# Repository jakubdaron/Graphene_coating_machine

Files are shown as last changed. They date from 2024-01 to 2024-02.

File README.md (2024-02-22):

429411629_411741121228787_1074731807515884978_n (1)

**Graphene coating machine**

In this project we showcase a budget machine for creating graphene coatings on work surfaces of wire forming die based on technology described in patent  PL 239477.

The machine was built using budget and easly accessible components as well as 3D printed parts. 
It consists of a linear Z-axis and a turntable that is outfited with pressure sensor and allows for full 360deg rotation.
Z axis allows the electrode to put pressure on the die in range of 0,5 - 5kg, set by user. 
Pressure sensor readings allow the pressure to be in range of 5 - 15% error tolerance depending on the quallity of sensor calibration.

DISCLAIMER:
Presented machine is an academic proof of concept and is not sutable for industrial aplication in it's current version. 
This project was done on behest and with guidance from patent owner for the technology as a proof of concept.

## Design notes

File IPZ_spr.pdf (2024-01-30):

# Urządzenie do nakładania powłok grafenowych na powierzchnię roboczą ciągadła stalowego

# Interdyscyplinarny projekt zespołowy 2023/24 Mechatronika - II stopień

Prowadzący Projektu:
Dr hab. inż. Zbigniew Zimniak Autorzy:
Jakub Daroń
Michał Dubaniewicz
Piotr Grabowski
Wojciech Kargul
Jan Konior
Mateusz Lisoń

## 1. Wstęp

W procesie ciągnienia drutów na ciągarkach wykorzystywane narzędzia – ciągadła – są poddawane są znaczącym siłą i z czasem degenerują pod wpływem ścierania. Z tego tytułu stosuje się materiały wysoce odporne na ścieranie do pokrycia powierzchni stożka roboczego. Typowe stosowane materiały to diament i węgliki spiekane. Na Rys. 1 przedstawiono schemat budowy ciągadła.

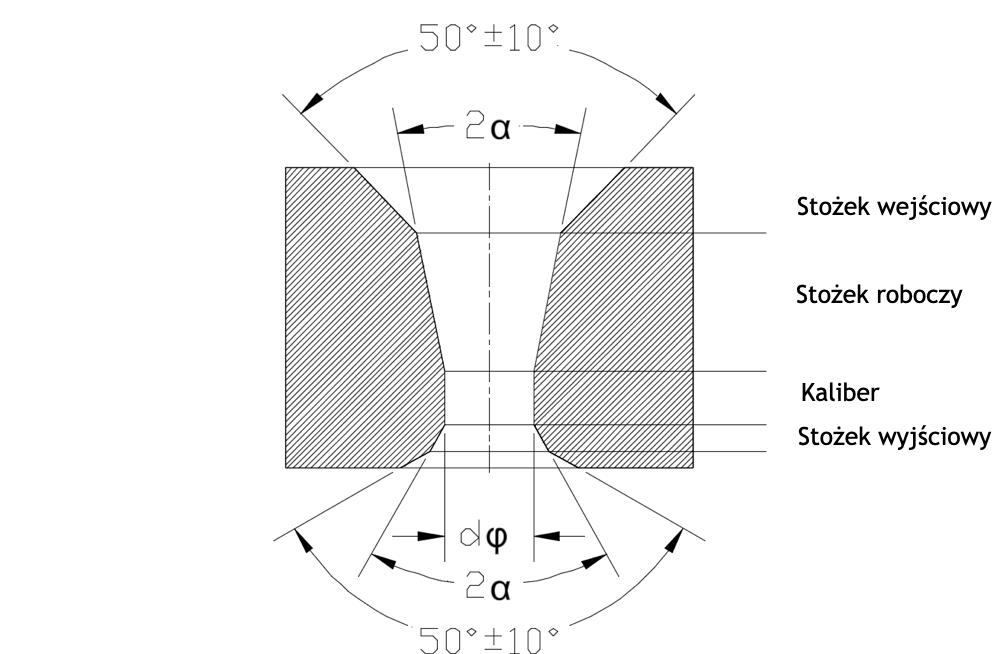
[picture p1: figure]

Rysunek 1 - schemat budowy ciągadła
Prowadzący projektu, dr hab. inż. Zbigniew Zimniak w swoim patencie nr PL 239477, zatytułowanym „Sposób wytwarzania trwałych cienkowarstwowych pokryć grafenowych na metalach” opisał metodę wytwarzania pokryć cienkowarstwowych z grafenu na metalach. Jak wiadomo grafen jest materiałem wysoce odpornym na ścieranie, w ramach projektu postanowiono zatem stworzyć urządzenie które pozwoli wykorzystać tą metodę do wykonywania powłok na elementach roboczych ciągadła stalowego.
W związku z tym określono następujące założenia projektowe:
- Minimalizacja kosztów – ze względu na brak funduszy wszystkie środki pochodzić będą z kieszeni wykonawców, określono budżet na poziomie ok. 600 zł.
- Maksymalizacja wykorzystania elementów typowych i wykonanych metodą druku 3D – ze względu na charakter naukowy budowanego urządzenia i niski budżet pewne elementy mogą wymagać wymiany lub modyfikacji z czasem. Zastosowanie druku 3D i elementów typowych ułatwi pracę w tego typu sytuacjach.
- 1 oś przesuwu liniowego pozwalająca uzyskać nacisk ok. 2kg, siła nacisku musi być sterowalna w pewnym zakresie – Parametry nacisku są powiązane z wymaganiami procesu nakładania powłok.

- 1 oś obrotowa – umożliwia obrót ciągadła i podział obrotu na x cykli w celu powtórzenia operacji pokrywania w innych pozycjach.
- Operacja półautomatyczna – ze względu na to że zasilacz generujący wyładowanie elektryczne jest stosowany również w innych instalacjach zdecydowano że nie będzie on sterowany z urządzenia tylko wyzwalany ręcznie.
- Sterowanie za pomocą aplikacji okienkowej – ze względu na ograniczanie kosztów zrezygnowano z fizycznego sterowania.

## 2. Przegląd Rozwiązań

Ze względu na to że urządzenie nie realizuje szeroko rozpowszechnionego procesu, nie ma rozwiązań które można wykorzystać jako bezpośrednie odniesienie. Z tego powodu poszczególne elementy projektu odnoszono do różnych urządzeń.
W przypadku osi przesuwu liniowego, jednym z bardziej powszechnych rozwiązań tego typu są drukarki 3D. Wykorzystują one śruby trapezowa lub kulowe drobnozwojne w celu uzyskania dokładności pozycjonowania. Całość jest napędzana napędami krokowymi. Przykład takiego urządzenia przedstawiono na Rys. 2.

Rysunek 2 - Przykładowa drukarka 3D (Prusa MINI+)

Innym przykładem urządzenia które przewijało się jako potencjalna inspiracja w przypadku przesuwu liniowego jest wiertarka kolumnowa, ze względu na to że są to konstrukcje przenoszące duże obciążenia. Na Rys. 3 przedstawiono przykładową konstrukcję.

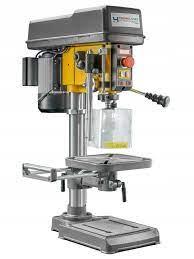
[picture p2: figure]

Rysunek 3 - przykładowa wiertarka kolumnowa
Ostatecznie, w przypadku projektowanego urządzenia konieczne będzie częściowe połączenie konkretnych cech obu rozwiązań – precyzji drukarek 3D i wytrzymałości którą cechuje się konstrukcja wiertarki kolumnowej.

W przypadku osi obrotowej, ciekawą inspiracją były stoły obrotowe do frezarek CNC (Rys. 4). Urządzenia te pozwalają uzyskać obrót o zadany kąt i są sterowane. Kwestią którą należy rozwiązać w celu adaptacji tego typu rozwiązania do projektu jest rozmiar i metoda mocowania obiektu w sposób zapewniający centryczność ciągadła i elektrody.

Rysunek 4 - przykładowy stół obrotowy do frezarki CNC

W przypadku pomiaru nacisku, na rynku są dostępne 2 główne rodzaje rozwiązań – czujniki membranowe i belki tensometryczne (Rys. 5). Belki tensometryczne pozwalają na uzyskanie odczytów dla dużych nacisków (powyżej 10 kg), natomiast zajmują dużo miejsca i w zastosowaniu takim jak w projekcie konieczne byłoby wykorzystanie minimum 2 takich belek. Czujniki membranowe z kolei są nieco bardziej wrażliwe na punkt przyłożenia siły i z reguły mają niższe zakresy pracy.

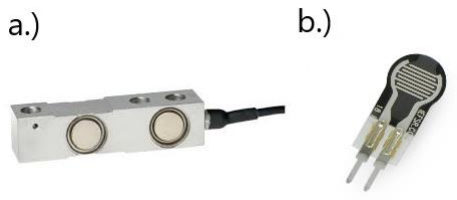
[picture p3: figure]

Rysunek 5 - a.) belka tensometryczna b.) czujnik membranowy

## 3. Sekcja Mechaniczna

### a. Ruch w osi pionowej

Pierwszym zagadnieniem mechanicznym do realizacji było zapewnienie ruchu elektrody w osi pionowej, jednocześnie z możliwością generowania jej docisku do ciągadła z siłą odpowiadającą wartości 2 [N]. W tym celu zamówiono prowadnicę liniową THK KR20A 200mm CNC o skoku śruby wynoszącym 1[mm] (Rys. 6). Ruch obrotowy śruby będzie generowany za pomocą silnika krokowego JK42HS40 – 0404, który zostanie szerzej przedstawiony w sekcji elektronicznej.

Rysunek 6 - Prowadnica liniowa THK KR20A 200 mm CNC
Szkieletem całego układu jest profil aluminiowy, do którego przymocowana została prowadnica oraz mocowanie stalowe typu L do silnika krokowego (Rys. 7). Napęd na prowadnicę przenoszony będzie za pomocą sprzęgła osiowo elastycznego (Rys. 8).

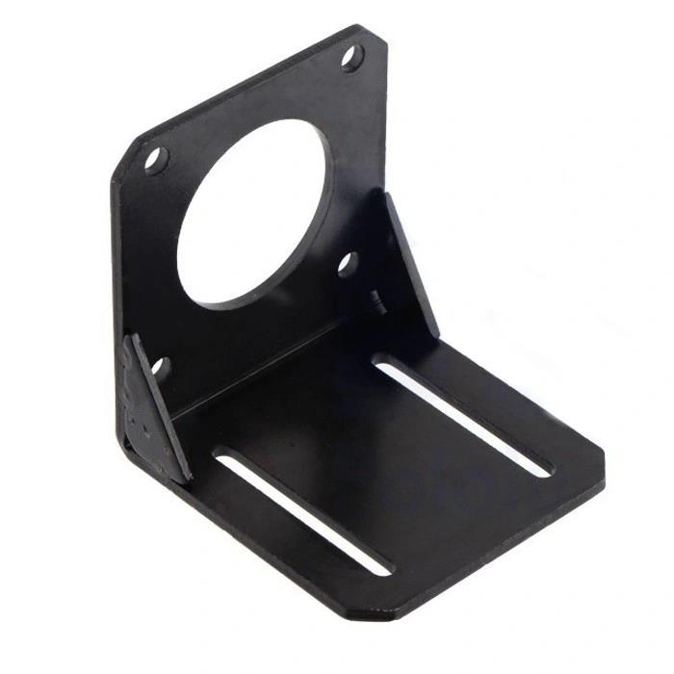
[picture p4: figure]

Rysunek 7 - Stalowe mocowanie silnika typu L

Rysunek 8 - Sprzęgło osiowo elastyczne do silnika krokowego

### b. Koncepcje ramienia trzymającego elektrodę

Kolejnym założeniem do realizacji była stabilizacja, przełożenie ruchu w osi pionowej na elektrodę oraz utrzymanie jej w osiowości z ciągadłem. W tym celu zaprojektowano ramię, które zostanie połączone z prowadnicą oraz utrzyma elektrodę w odpowiedniej pozycji. Pierwsza koncepcja ramienia zakładała, że w pełni zostanie ono wydrukowane za pomocą drukarki 3D, ze względu na fakt, że elektroda musi zostać odizolowana od reszty układu, ponieważ ma przez nią przepływać prąd. Założono, że ramię będzie składać się z dwóch elementów, dzięki czemu możliwa była regulacja jego długości. Zamodelowane rozwiązanie przedstawiono na Rys. 9.

Rysunek 9 - Pierwsza koncepcja ramienia
Szybko jednak zrezygnowano z tego pomysłu na dużą podatność tego układu, co nie zapewniało odpowiedniej stabilności oraz wytrzymałości. Wtedy zrodziła się myśl wykorzystania profilu aluminiowego jako ramienia, aby bardziej ustabilizować elektrodę. Tak więc powstało nowe rozwiązanie przedstawione na Rys. 10.

Rysunek 10 - Druga koncepcja ramienia

Pozostał wówczas problem z zamocowaniem profilu do prowadnicy. W tym celu zaprojektowano specjalistyczny uchwyt wydrukowany na drukarce 3D (Rys. 11).

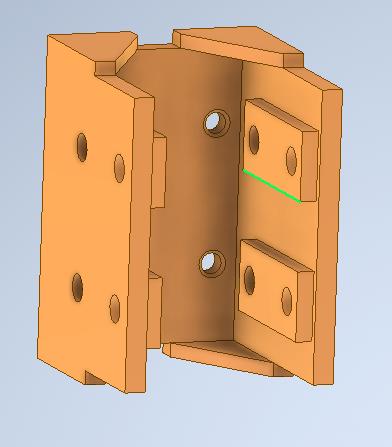
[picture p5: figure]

Rysunek 11 - Mocowanie ramienia do prowadnicy

W ostateczności model został zrewidowany tak aby uwzględnić zaprojektowane mocowanie. Bazując na tym projekcie wykonano fizyczne ramie. Model po poprawkach przedstawiono na Rys. 12, a fizyczną realizację na Rys. 13.

Rysunek 12 - Finalna koncepcja ramienia

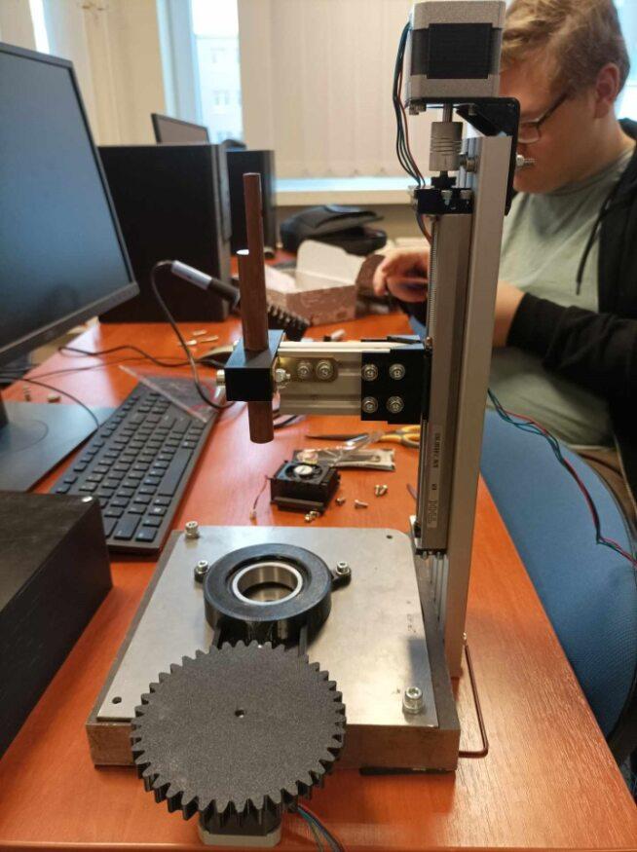
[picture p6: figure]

Rysunek 13 - Realizacja ramienia z prowadnicą zamocowana na ramie układu

### c. Stół obrotowy pod ciągadło

Ostatnim zagadnieniem do rozpatrzenia było umiejscowienie ciągadła oraz umożliwienie mu obrotu. W tym celu zaprojektowano stół obrotowy, którego ruch wykonywany będzie za pomocą takiego samego silnika krokowego, jak w przypadku prowadnicy. Moment obrotowy przenoszony będzie za pomocą przekładni zębatej. Przełożenie obliczono jako stosunek liczby zębów obu kół zębatych, korzystając ze wzoru:

i =

z2
z1
gdzie:
z1 – liczba zębów koła napędzającego
z2 – liczba zębów koła napędzanego
W wyniku czego otrzymano następujące przełożenie:

i =

64
40 = 1,6

Początkowa koncepcja stołu została przedstawiona na Rys 14.

Rysunek 14 Początkowa koncepcja mocowania ciągadła
W dalszych etapach rozwoju koncepcji, ze względu na dostępność i ułatwienie centrowania osiowego względem elektrody, zrezygnowano z imadła zaciskowego, a w jego miejsce pojawił się uchwyt trójszczękowy (Rys 15).

Rysunek 15 - Ciągadło w uchwycie trójszczękowym
Układ wyposażony został w łożysko kulkowe jednorzędowe 6008 2RS (Rys. 16), którego zadaniem jest przede wszystkim przenoszenie obciążeń osiowych, spowodowanych dociskiem elektrody na ciągadło.

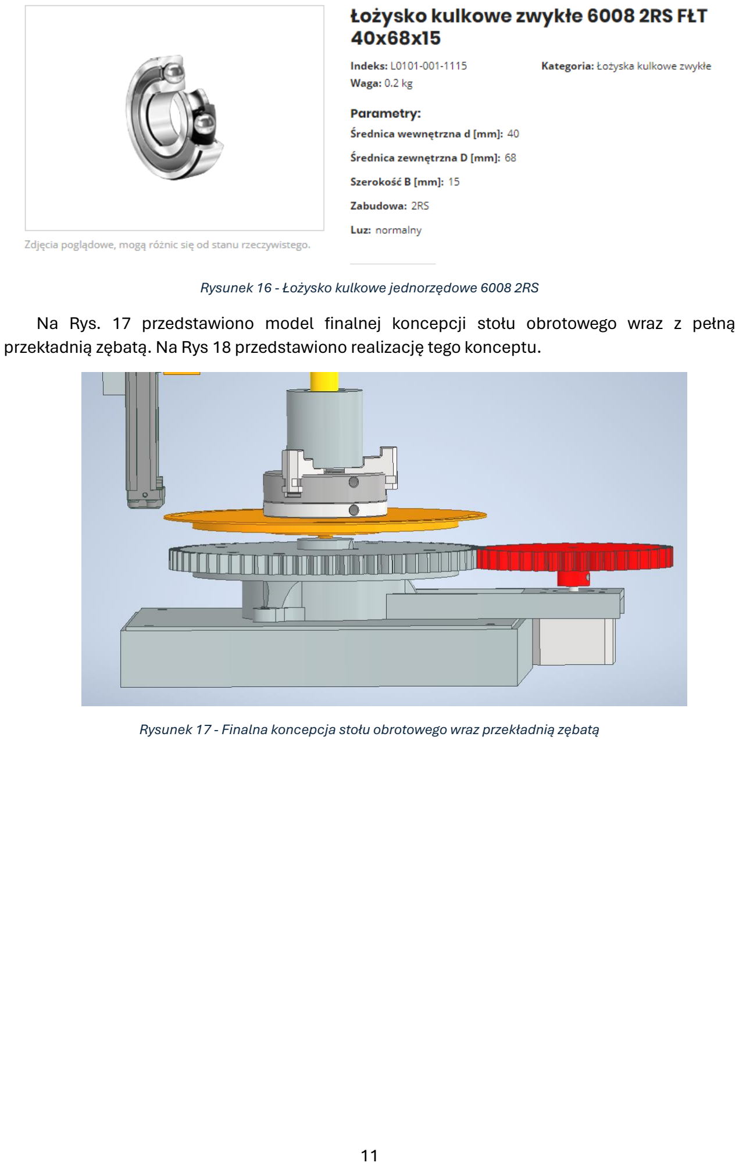
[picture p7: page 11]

Rysunek 16 - Łożysko kulkowe jednorzędowe 6008 2RS
Na Rys. 17 przedstawiono model finalnej koncepcji stołu obrotowego wraz z pełną przekładnią zębatą. Na Rys 18 przedstawiono realizację tego konceptu.

Rysunek 17 - Finalna koncepcja stołu obrotowego wraz przekładnią zębatą

Rysunek 18 - Realizacja fizyczna stołu obrotowego

### d. Części niestandardowe

Ze względu na specyficzne cechy wymagane w projekcie sporo części zostało wykonane wg. dedykowanego projektu. Duża część elementów została wykonana za pomocą druku 3D. Na Rys. 14 przedstawiono rysunek złożeniowy układu. Poniżej, na Rys. 19 – Rys. 29 przedstawiono rysunki wykonawcze części niestandardowych.

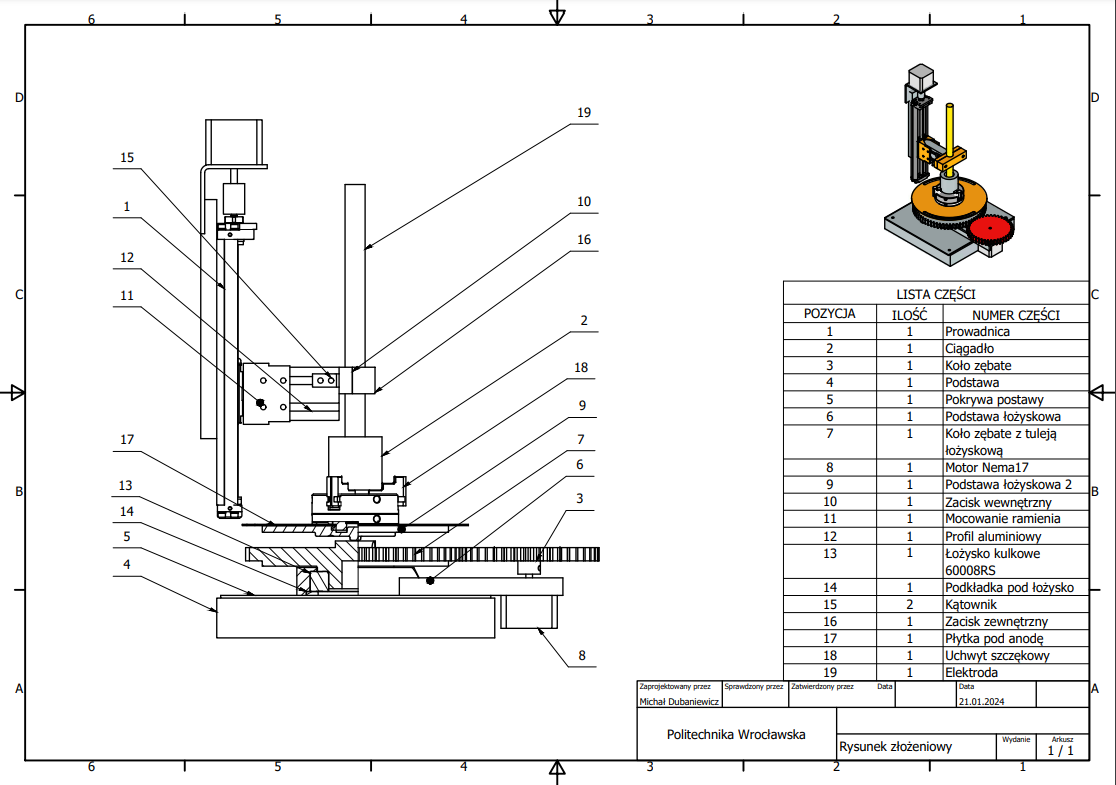
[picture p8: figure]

13

Rysunek 19 - Rysunek złożeniowy układu

14

Rysunek 20 - Rysunek wykonawczy trzonu elektrody

15

Rysunek 21 - Rysunek wykonawczy koła zębatego z tuleją łożyskową

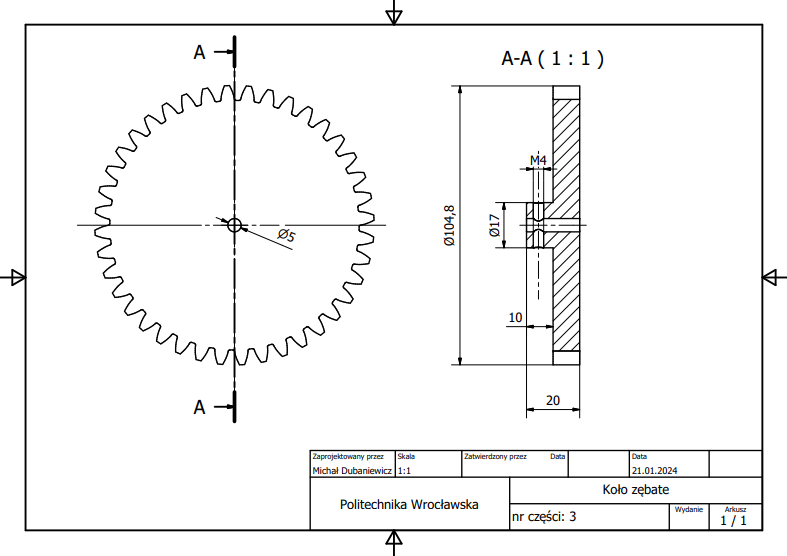
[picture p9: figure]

16

Rysunek 22 - Rysunek wykonawczy koła zębatego

Rysunek 23 - Rysunek wykonawczy mocowania ramienia

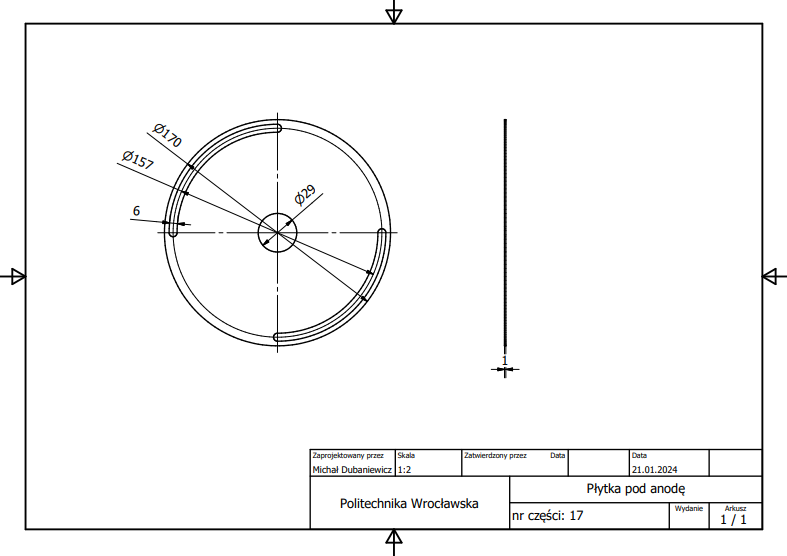
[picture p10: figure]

18

Rysunek 24 - Rysunek wykonawczy płytki montażowej do anody

19

Rysunek 25 - Rysunek wykonawczy podstawy łożyskowej

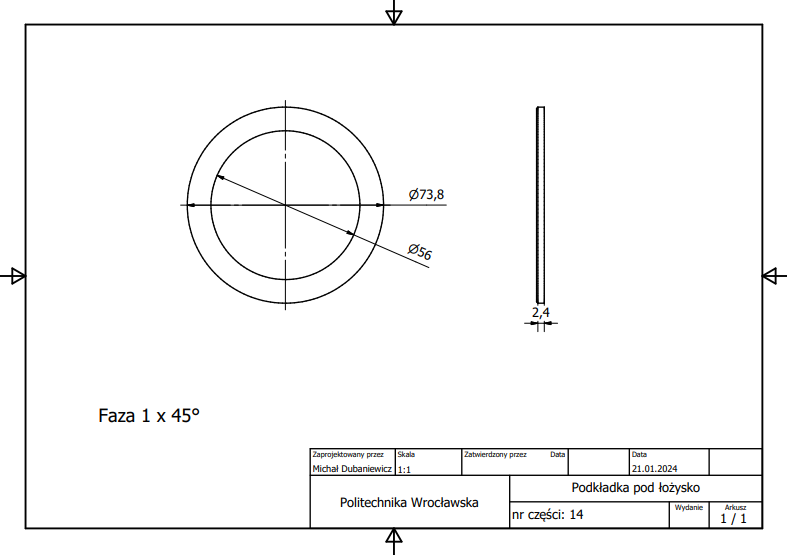
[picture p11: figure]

20

Rysunek 26 - Rysunek wykonawczy podkładki pod łożysko

21

Rysunek 27 - Rysunek wykonawczy stolika

Rysunek 28 - Rysunek wykonawczy zacisku zewnętrznego elektrody

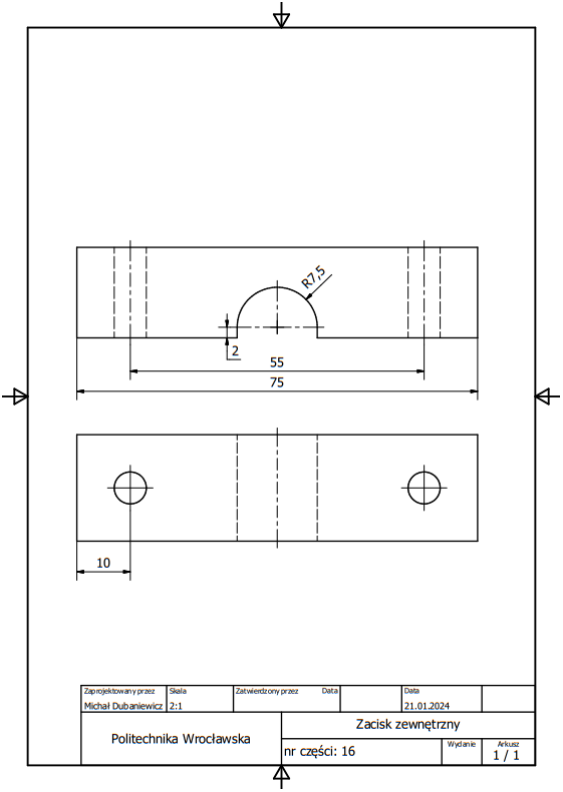
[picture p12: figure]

Rysunek 29 - Rysunek wykonawczy zacisku wewnętrznego elektrody

## 4. Sekcja Elektroniczna

### a. Układ elektroniczny

W celu realizacji pracy którą wykonywać ma urządzenie dobrano napędy z uwagi na niezbędne parametry mechaniczne. Dobrane zostały napędy krokowe JK42HS40-0404 (Rys. 30) które mają możliwość utrzymania momentu 0,25Nm i dokładność 200 kroków na obrót z możliwością uzyskania większego podziału za pomocą funkcji mikrostep. Napędy te zasilane są napięciem 12V i pobierając 0,4A na cewkę.

Rysunek 30 - silnik JK42HS40-0404
Bazując na niezbędnych wymaganiach z punktu widzenia mechaniki układu dobrano również czujnik nacisku. Wybrano czujnik CP15-151NS (Rys.31), jest to czujnik membranowy o zakresie pomiarowym na poziomie 0,2 – 100N, co sprawia że przy odpowiednim dobraniu zakresu pomiarowego możliwe będzie pomiar w nacisku przy sile ok. 2kg które ma być domyślnym naciskiem urządzenia.

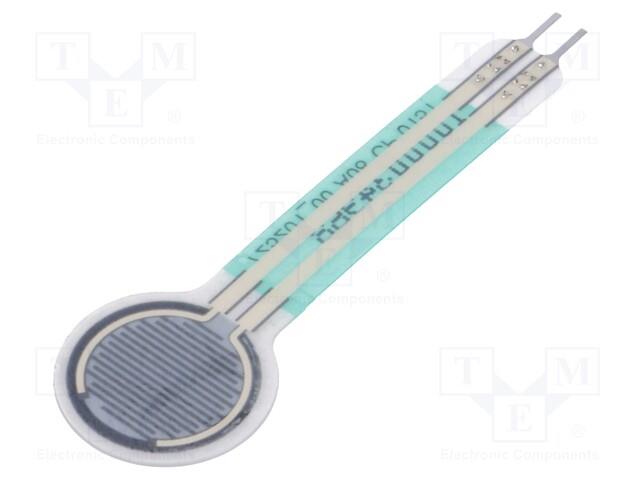
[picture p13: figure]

Rysunek 31 – Czujnik CP15-151NS

Pozostałe elementy dobrano kierując się głównie ceną i zgodnością parametrów elektrycznych. Do roli jednostki głównej wybrano Arduino UNO (Rys. 32) wraz z rozszerzeniem Arduino CNC Shield (Rys. 27) które jest wyspecjalizowanym, gotowym układem umożliwiającym sterowanie silnikami krokowymi, co oszczędza projektowania złożonych układów elektronicznych.

Rysunek 32 - a.) Arduino UNO b.) Arduino CNC Shield

Do pracy w CNC Shield konieczne są sterowniki silników krokowych. Zdecydowano się na wykorzystanie układów typu A4988 (Rys.33). Są to bardzo podstawowe konstrukcje, natomiast mają możliwość obsługi napędów pracujących na napięciach 8-35V i pobierających do 1A na cewkę oraz pozwalają na obsługę microstep do rozdzielczości 1/16 kroku. Jest to układ jak najbardziej wystarczający w tym przypadku.

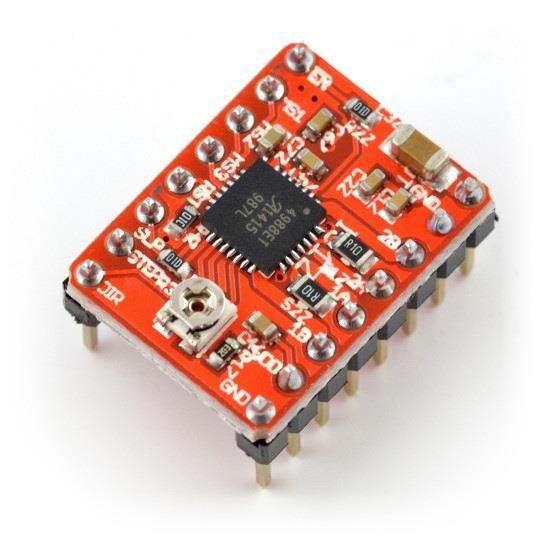
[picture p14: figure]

Rysunek 33 - Układ A4988

Dobrany zasilacz musiał mieć możliwość zasilenia napędów oraz posiadać odpowiedni zapas amperażu. Z tego powodu dobrano zasilacz Milio SS-60-12 (Rys. 34). Jest to prosta jednostka o mocy 60W oferująca na wyjściu prąd stały o napięciu 12VDC o natężeniu do 5A.

Rysunek 34 - Zasilacz Milio SS-60-12
Całość została połączona zgodnie ze schematem na Rys 35. Jak można zobaczyć na schemacie, dodany został przycisk ON/OFF umożliwiający włączenie i wyłączenie układu. Należy zaznaczyć że ze względu na wybraną metodę obsługi (aplikacja okienkowa) zdecydowano się na nie podłączanie Arduino UNO do głównego zasilacza 12V. Będzie ono zasilane z potu USB, jako że podłączenie z komputerem jest wymagane.

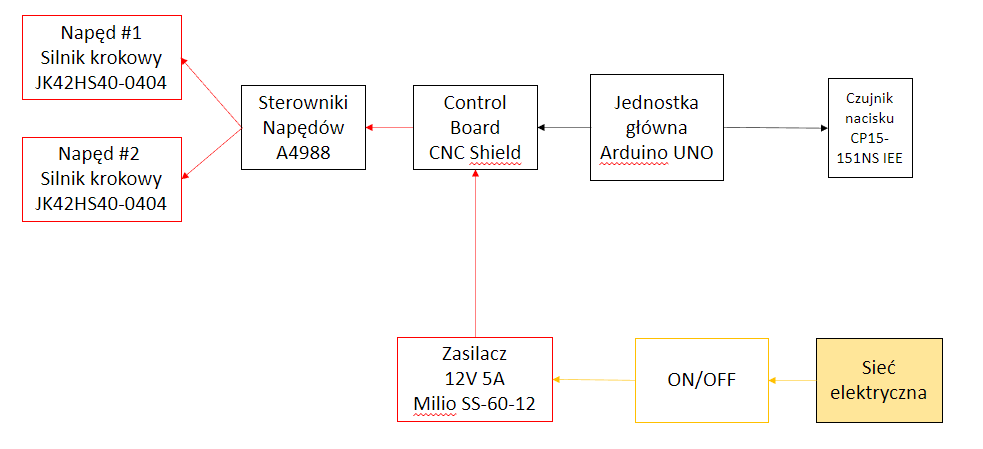
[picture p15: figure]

Rysunek 35 - Schemat ideowy układu elektronicznego

Na Rys. 36 i Rys. 37 przedstawiono położenie elementów na gotowej mechanice.

Rysunek 36 - Rozmieszczenie elementów wewnątrz obudowy

Rysunek 37 - elementy układu na ramie urządzenia

### b. Podłączenie czujnika nacisku

Podłączenie czujnika nacisku jest dość specyficznym zadaniem. Jest to czujnik analogowy, który opiera się na zmianie rezystancji membrany pod wpływem nacisku. Czujnik jest jednym z wyprowadzeń podpinany do zasilania, a drugim do wejścia analogowego. Dodatkowo konieczne jest poprowadzenie mostka między przewodem idącym na wejście analogowe, a masą przez rezystor. Zmiana wartości rezystancji tego rezystora wpływa na zakres pomiarowy, należy więc przeprowadzić kalibrację i dobrać ją odpowiednio. Poniżej na Rys. 38 przedstawiono podłączenie czujnika.

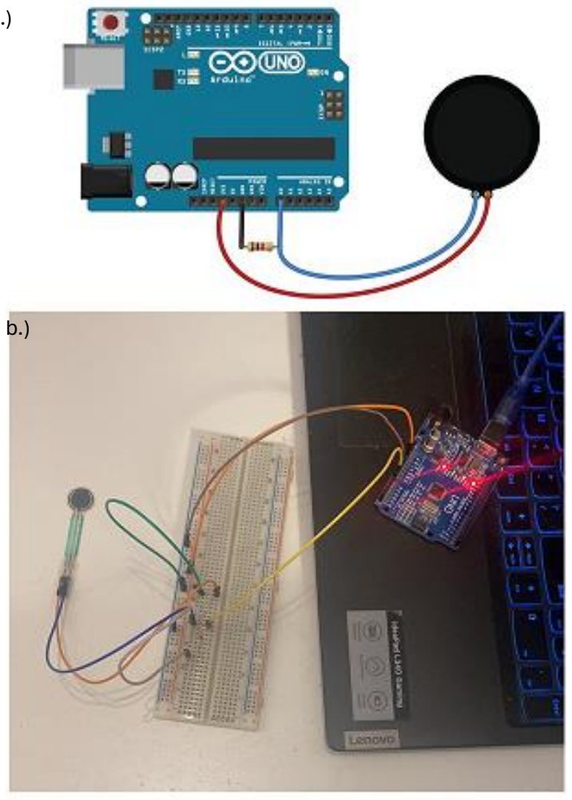
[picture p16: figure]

Rysunek 38 - a.) schemat podłączenia b.) rzeczywista realizacja podłączenia

a.)

### c. Obudowa

W ramach zabezpieczenia układu przed wpływem otoczenia oraz zapewnienia bezpieczeństwa użytkownikom zaprojektowano obudowę z tworzywa, wykonaną metodą druku 3D. Na Rys 39 przedstawiono finalny rezultat. Na Rys. 40 i 41 przedstawiono rysunki wykonawcze obudowy.

Rysunek 39 – Obudowa

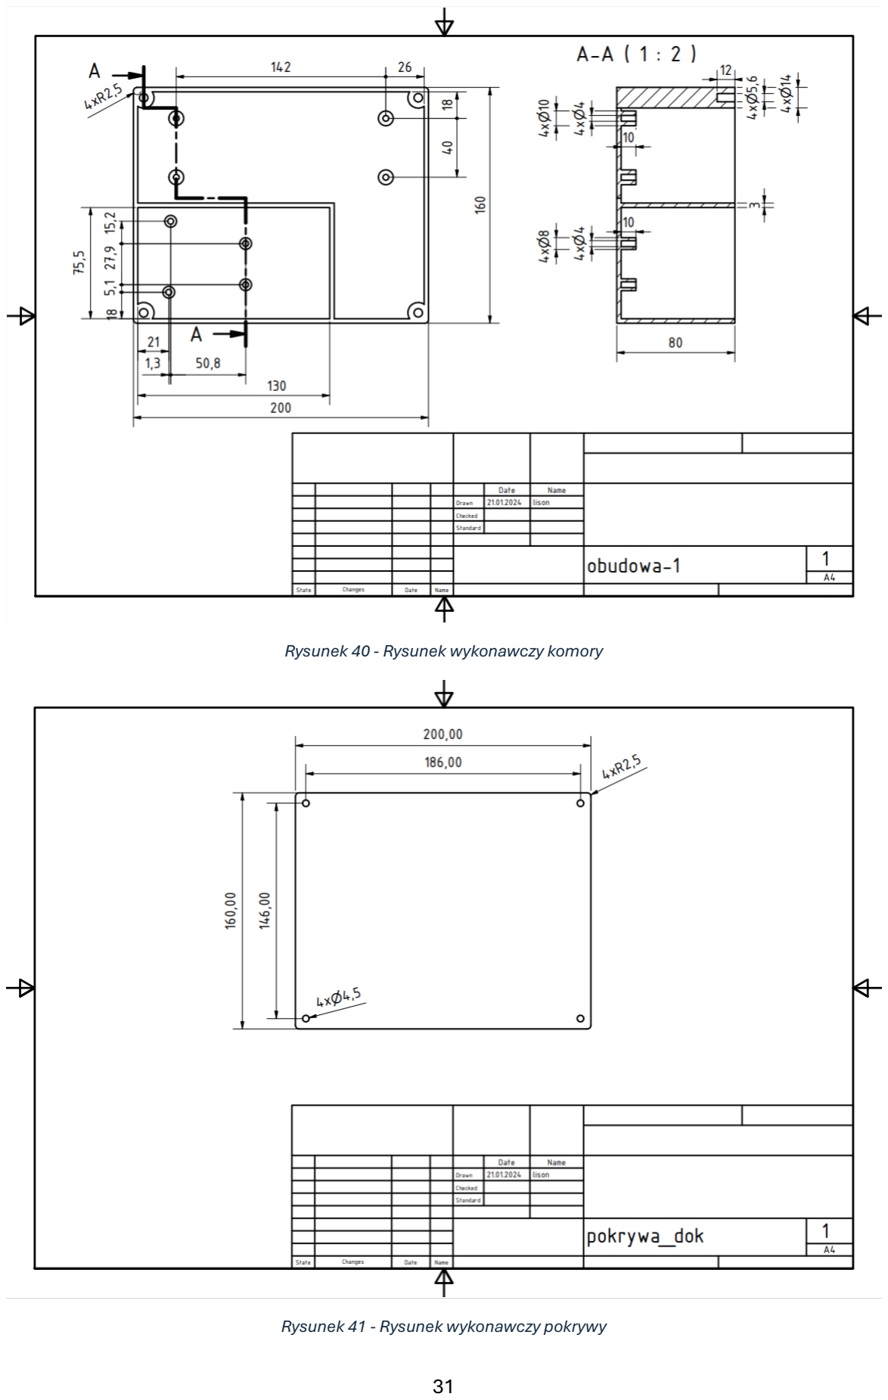
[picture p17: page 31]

Rysunek 40 - Rysunek wykonawczy komory

Rysunek 41 - Rysunek wykonawczy pokrywy

## 5. Sekcja programistyczna

### a. Koncepcje i zastosowane technologie

Początkowo założono 3 koncepcje realizacji sterowania procesem:
- zbudowanie fizycznego panelu obsługi z przyciskami, kontrolkami i małymi wyświetlaczami LCD.
- zakupienie dotykowego wyświetlacza LCD, który mógłby posłużyć jako panel sterowania.
- stworzenie aplikacji do obsługi procesu, którą można uruchomić na dowolnym komputerze.

Finalny wybór padł na koncepcję stworzenia aplikacji, co potwierdzają rozważania na temat następujących aspektów:
- aspekt finansów i dostępności – zamiast kupowania nowych komponentów wykorzystywane są komputery znajdujące się w laboratorium, bądź komputer prywatny osoby obsługującej urządzenie.
- aspekt możliwych modyfikacji – aplikację komputerowa dużo łatwiej i szybciej można zmodyfikować, niż przebudowywać cały fizyczny panel sterowania.
- aspekt czasu – postawienie na rozwiązanie w pełni software’owe pozwala na zaoszczędzenie czasu związanym z fizycznym budowaniem panelu obsługi procesu.

Do budowy aplikacji wykorzystano język programowania Python wraz z 3 bibliotekami rozszerzającymi funkcjonalności:
- -PyQt5 – biblioteka wykorzystana do stworzenia całego interfejsu graficznego aplikacji w formie okienek.
- pyserial – biblioteka wykorzystana do komunikacji z modułem Ardunio (realizacja polecenia programu w zbudowanym urządzeniu).
- pyinstaller – biblioteka wykorzystana do konwersji kodu w języku Python do pliku wykonywalnego w formacie exe, który jesteśmy w stanie uruchomić na każdym komputerze z zainstalowanym systemem operacyjnym Windows.

### b. Interfejs użytkownika

Interfejs użytkownika wykonano w pełni z wykorzystaniem biblioteki PyQt5, rozszerzającej podstawowe funkcjonalności języka programowania Python. Użycie przytoczonej biblioteki pozwoliło na stworzenie przejrzystego interfejsu w formie okienek. Projektowanie okienek przeprowadzono w programie „Qt designer” (Rys. 42), gdzie zrealizowano całą warstwę graficzną aplikacji:
- modyfikacja kolorów i wielkości okienek oraz znajdujących się w nich napisów.
- modyfikacja kolorów, wielkości i oznaczeń przycisków.
- wstawienie pól do zmiany parametrów procesu.
- ograniczenia wyjścia z poszczególnych okienek.

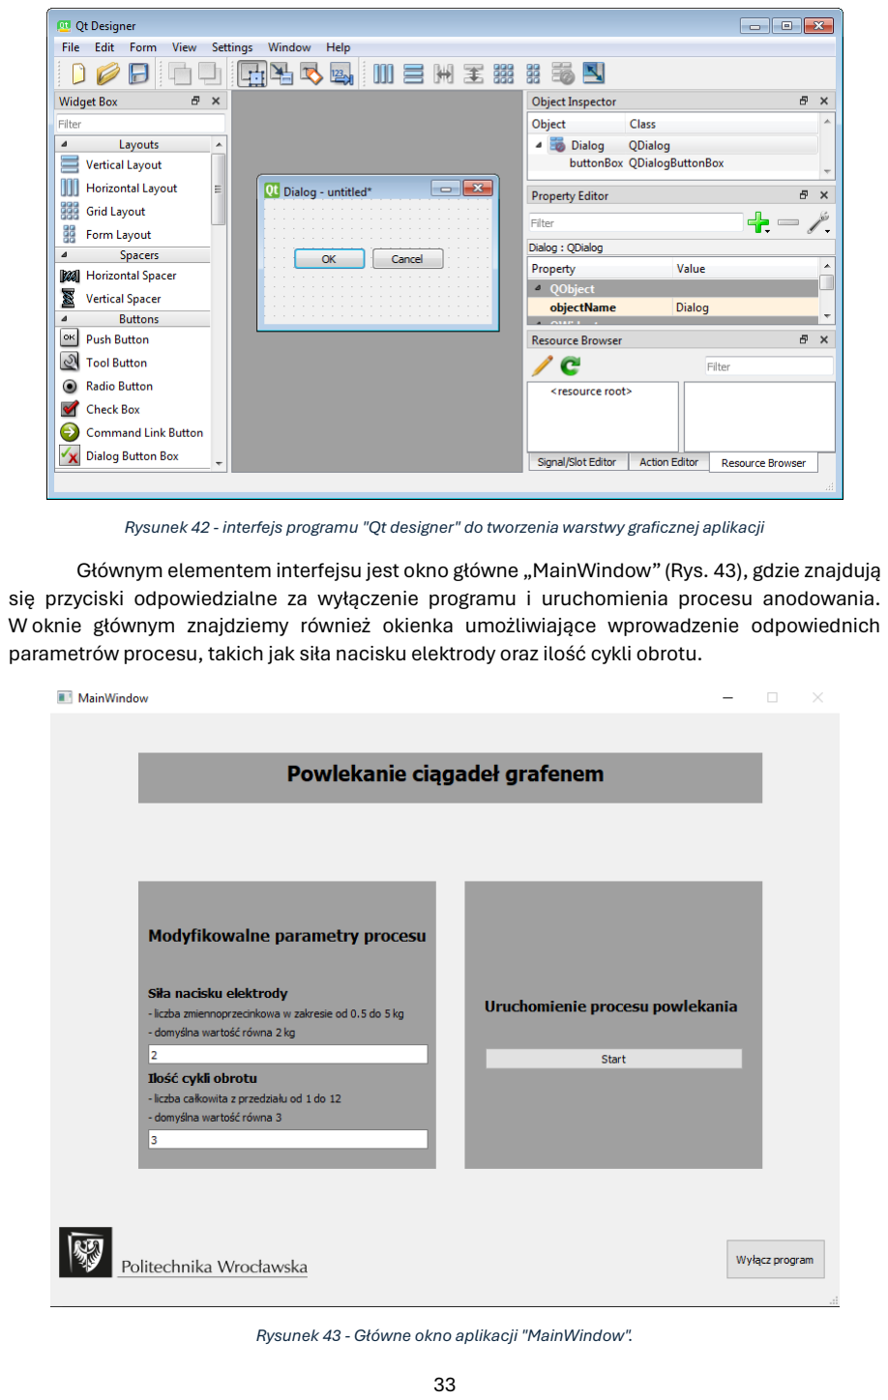
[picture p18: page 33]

Rysunek 42 - interfejs programu "Qt designer" do tworzenia warstwy graficznej aplikacji
Głównym elementem interfejsu jest okno główne „MainWindow” (Rys. 43), gdzie znajdują się przyciski odpowiedzialne za wyłączenie programu i uruchomienia procesu anodowania. W oknie głównym znajdziemy również okienka umożliwiające wprowadzenie odpowiednich parametrów procesu, takich jak siła nacisku elektrody oraz ilość cykli obrotu.

Rysunek 43 - Główne okno aplikacji "MainWindow".

Dodatkowo w trakcie obsługi aplikacji pojawiają się okienka informacyjne z przyciskami pozwalającymi na dalszą realizację programu (Rys. 44), bądź bez nich (Rys. 45)

Rysunek 44 - Przykładowe okno informacyjne z przyciskiem do kontynuowania realizacji programu

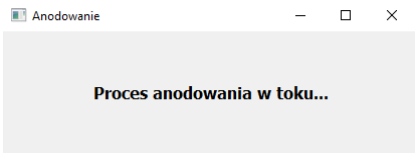
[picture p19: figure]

Rysunek 45 - Przykładowe okno informacyjne bez przycisku

### c. Obsługa programu

i. Uruchomienie programu
Aby uruchomić program rozpakowujemy paczkę z folderem zawierającym program „IPZ_proj.zip” na dysku komputera. W rozpakowanym folderze wyszukujemy pliku uruchomieniowego programu pod nazwą „init.exe” (Rys.46), którego uruchomienie pozwala nam na pracę z aplikacją.

Rysunek 46 - Widok folderu z podkreślonym plikiem uruchomieniowym aplikacji "init.exe"

ii. Wyłączenie programu
Wyłączenie programu z poziomu aplikacji możliwe jest do zrealizowania tylko w momencie znajdowania się w oknie głównym aplikacji (Rys. 47) przyciskiem „Wyłącz program”, zlokalizowanym w prawym dolnym rogu głównego okna aplikacji.

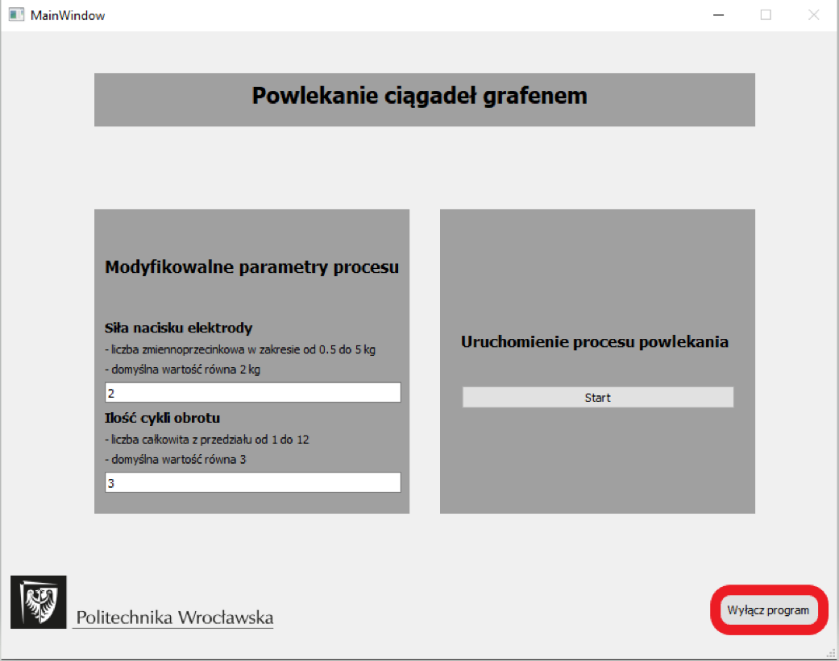
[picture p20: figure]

Rysunek 47 - Widok okna głównego z oznaczonym na czerwono przyciskiem „Wyłącz program” służącym do wyjścia z programu.
iii. Realizacja procesu
Na samym początku realizacji procesu sprawdzamy określamy wartości modyfikowalnych parametrów za pomocą dwóch okienek umieszczonych po lewej stronie okna głównego (Rys. 48). Domyślnie owe parametry wynoszą odpowiednio:
- 2kg siły nacisku elektrody
- 3 cykle obrotu

Rysunek 48 - Widok okna głównego z oznaczonymi na żółto okienkami służącymi do modyfikacji parametrów procesu.
Jeśli chcemy wykonać proces z wykorzystaniem innych wartości parametrów niż domyślne, wystarczy usunąć w okienku wartość domyślną i wpisać wartość własną (należy pamiętać aby wartość własna była zgodna z opisem znajdującym się nad okienkiem konkretnego modyfikowalnego parametru!).
Przed uruchomieniem procesu powinniśmy upewnić się, że przedmiot do anodowania został poprawnie umieszczony w szczękach stołu maszyny. Uruchomienie procesu zaczynamy poprzez naciśnięcie przycisku „Start”, znajdującego się po prawej stronie okna głównego aplikacji (Rys. 49).

Rysunek 49 - Widok okna głównego z oznaczonym na niebiesko przyciskiem „Start”, służącym do uruchomienia procesu.
Obsługę procesu anodowania zapewniają wyświetlające się komunikaty. O trwaniu procesu użytkownika informuje poniższy komunikat (Rys. 50).

Rysunek 50 - Okno informacyjne o realizacji procesu anodowania.
W trakcie realizacji procesu pojawiają się również komunikaty, które informują użytkownika o wymaganej fizycznej interakcji, takie jak uzupełnienie warstwy grafenu oraz uruchomienie elektrody (Rys. 51).

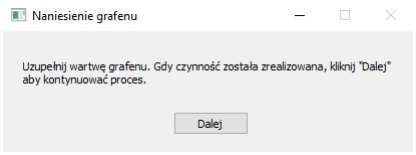
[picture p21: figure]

Rysunek 51 - Okno informacyjne o uzupełnieniu warstwy grafenu.

### d. Zabezpieczenia oprogramowania

W przypadku wprowadzenia nieprawidłowych danych w okienkach siły nacisku elektrody oraz ilości cyklów obrotu, następuje obsługa błędu w postaci resetu wartości w okienkach oraz wyświetlenia komunikatu poniżej (Rys. 52).

Rysunek 52 - Okno informacyjne z odniesieniem do wprowadzenia błędnych parametrów w programie.
W przypadku uruchomienia programu bez podłączenia urządzenia przez port USB do komputera, wyświetla się komunikat o braku połączenia urządzenia z komputerem (Rys. 53).

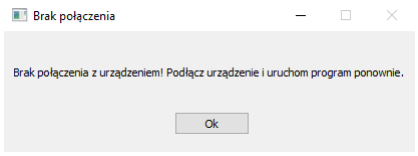
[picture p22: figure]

Rysunek 53 - Okno informacyjne z odniesieniem do braku połączenia urządzenia z komputerem.
W przypadku nie umieszczenia obiektu anodowanego na początku uruchomienia procesu anodowania następuje obsługa błędu w postaci zatrzymania procesu, wyświetlenia poniższego komunikatu oraz cofnięcia do okna głównego (Rys. 54).

Rysunek 54 - Okno informacyjne z odniesieniem do braku wykrycia obiektu do anodowania w imadle zaciskowym.

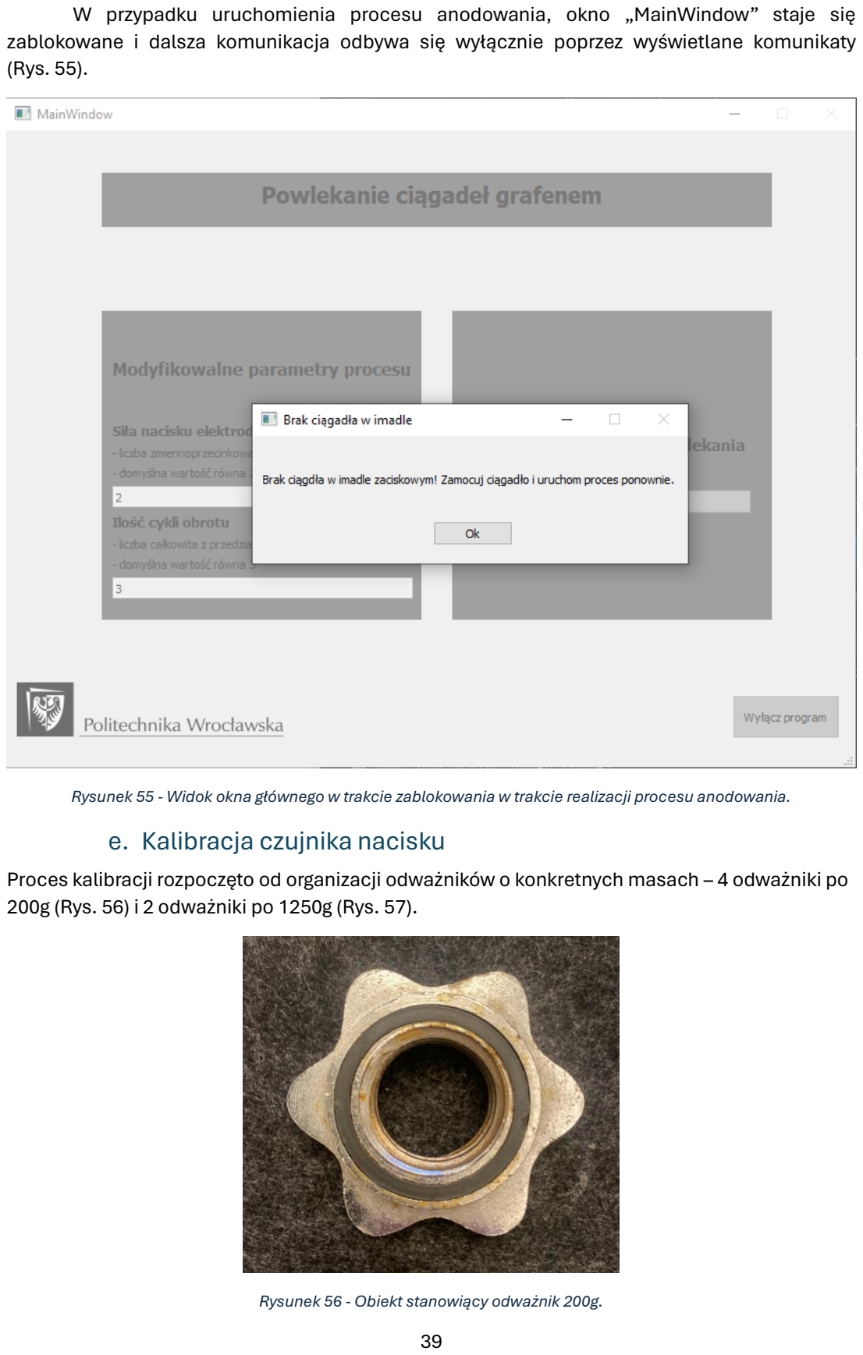
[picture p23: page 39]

W przypadku uruchomienia procesu anodowania, okno „MainWindow” staje się zablokowane i dalsza komunikacja odbywa się wyłącznie poprzez wyświetlane komunikaty (Rys. 55).

Rysunek 55 - Widok okna głównego w trakcie zablokowania w trakcie realizacji procesu anodowania.

### e. Kalibracja czujnika nacisku

Proces kalibracji rozpoczęto od organizacji odważników o konkretnych masach – 4 odważniki po 200g (Rys. 56) i 2 odważniki po 1250g (Rys. 57).

Rysunek 56 - Obiekt stanowiący odważnik 200g.

Rysunek 57 - Obiekt stanowiący odważnik 1250g.
Dla znanych mas przeprowadzono 4 serie pomiarowe podczas których odczytywano wartości czujnika, odpowiadające odpowiedniej kombinacji mas kalibracyjnych. Po przeprowadzeniu pomiarów, z czterech serii pomiarowych wyznaczono wartości średnich arytmetycznych, które posłużyły następnie do wyznaczenia krzywej kalibracji. Wszystkie dane pomiarowe zebrane zostały w tabeli 1.

Tabela 1 Dane uzyskane w celu wyznaczenia krzywej kalibracji.

masa(g) | pomiar 1 | pomiar 2 | pomiar 3 | pomiar 4 | średnia
0 | 0 | 0 | 0 | 0 | 0
200 | 145 | 142 | 146 | 144 | 144,25
400 | 173 | 178 | 180 | 200 | 182,75
600 | 245 | 238 | 242 | 239 | 241
800 | 278 | 314 | 276 | 351 | 304,75
1250 | 367 | 342 | 339 | 341 | 347,25
1450 | 393 | 388 | 390 | 389 | 390
1650 | 400 | 398 | 402 | 401 | 400,25
1850 | 427 | 428 | 429 | 427 | 427,75
2050 | 446 | 442 | 449 | 454 | 447,75
2500 | 462 | 469 | 467 | 467 | 466,25
2700 | 475 | 473 | 473 | 475 | 474
2900 | 478 | 480 | 479 | 481 | 479,5
3100 | 489 | 485 | 486 | 484 | 486

Krzywa kalibracji została wyznaczona poprzez zdefiniowanie wartości osi X jako wartości odpowiadające kombinacjom mas kalibracyjnych (żółta kolumna tabeli 1) oraz wartości osi Y jako wartości średnich arytmetycznych odczytu czujnika (zielona kolumna w tabeli 1).

Do wyznaczonej krzywej dopasowano linię trendu, która jest najbardziej zbliżona kształtem do krzywej kalibracyjnej. Na wykresie wyświetlono również wzór funkcji dopasowanej linii trendu do danych. Wzór funkcji dopasowanej linii trendu stanowi przelicznik do odczytu wartości rzeczywistych no podstawie odczytów czujnika w programie Arduino! Postać krzywej kalibracyjnej oraz dobranej do niej linii trendu przedstawiono na rysunku poniżej (Rys. 58).

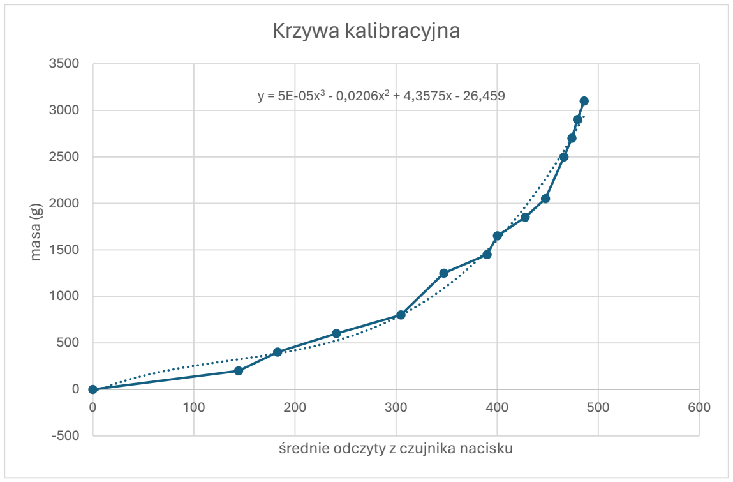
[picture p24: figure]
masa (g); średnie odczyty z czujnika nacisku; Krzywa kalibracyjna

Rysunek 58 - Krzywa kalibracyjna z dobraną linią trendu i wzorem funkcji linii trendu.
Ostatecznie w wyniku przeprowadzonej kalibracji udaje odczytać się wartości masy rzeczywistej z błędem na poziomie od 5% do 15%.
Aby zmodyfikować odczyty na podstawie własnej kalibracji należy podmienić postać funkcji przelicznika w następujących miejscach programu, realizowanego na Arduino (Podkreślone na rysunkach czerwoną linią):
- warunek pojedynczego odczytu masy po kalkulacji (Rys. 59)
- warunek poruszania w dół z limitem czujnika nacisku (Rys. 60)
- warunek precyzyjnego poruszania w dół w celu uzyskania najdokładniejszego możliwego odczytu (Rys. 61)

Rysunek 59 - Warunek pojedynczego odczytu masy po kalkulacji.

Rysunek 60 - Warunek poruszania w dół z limitem czujnika nacisku.

Rysunek 61 - Warunek precyzyjnego poruszania w dół w celu uzyskania najdokładniejszego możliwego odczytu.

### 6. Podsumowanie

W ramach projektu skonstruowano urządzenie które pozwala na realizację zaproponowanej technologii nakładania powłok grafenowych. Udało się zrealizować wszystkie przyjęte założenia projektowe. Należy natomiast zaznaczyć że ze względu na ograniczenia budżetowe urządzenie jest tylko i wyłącznie akademickim dowodem na wykonalność urządzenia realizującego zaproponowany proces i nie nadaje się do aplikacji przemysłowych. W celu uzyskania urządzenia nadającego się do bardziej wymagających aplikacji konieczne byłyby modyfikacje i usprawnienia podnoszące wytrzymałość, bezpieczeństwo, powtarzalność i dokładność.
Przykładowe usprawnienia mogą dotyczyć podniesienia dokładności pomiaru nacisku. Możliwe realizacje można podzielić na 3 kategorie:
- Zastosowanie dokładniejszych czujników
- Zastosowanie większej ilości czujników i uśrednienia odczytów
- Modyfikacja mechanizmu naciskającego na czujnik tak aby pozwalał na zachowanie pełnej liniowości
Wszystkie z powyższych możliwości zostały odrzucone ze względów finansowych.
Z tych samych powodów w konstrukcji wykorzystano dużą ilość elementów drukowanych w technologii druku 3D. W celu zwiększenia wytrzymałości wykorzystanie elementów z bardziej trwałych materiałów np. stali pozwoliłoby zwiększyć wytrzymałość.
Jak widać, zaprojektowane urządzenie nie jest perfekcyjnym rozwiązaniem, natomiast dowodzi że urządzenie takie jest wykonalne, nawet przy poważnych ograniczeniach budżetowych

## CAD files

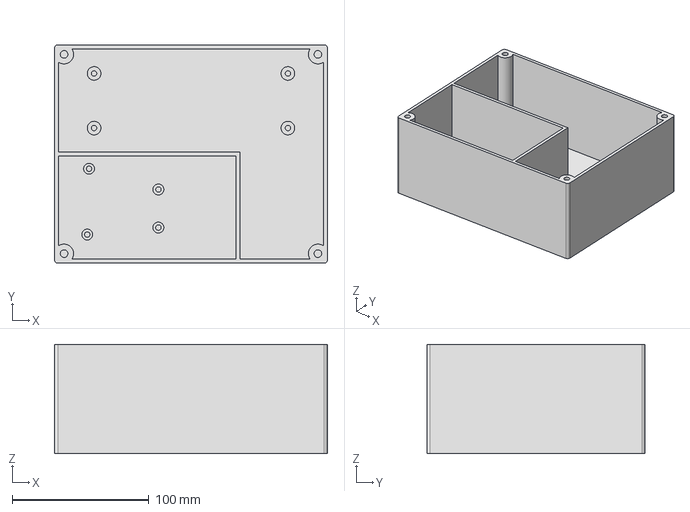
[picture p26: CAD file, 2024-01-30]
Step_models/electrical_components_enclosure/obudowa.stp
200.0 x 160.0 x 80.0 mm

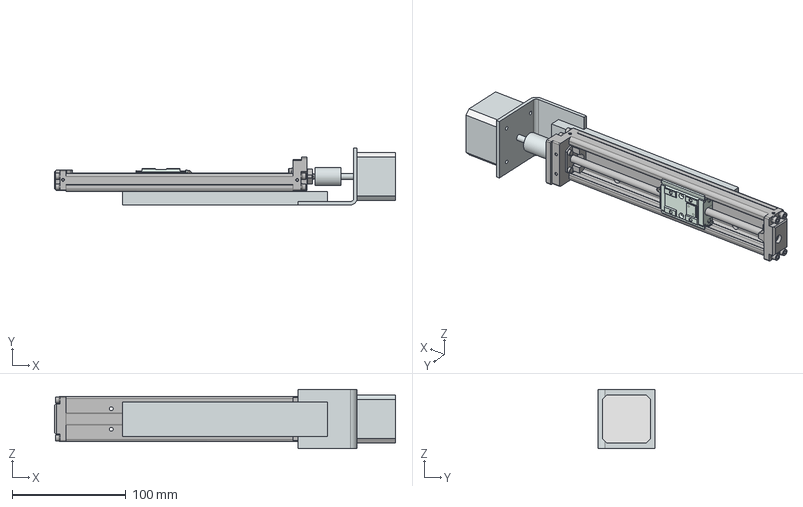
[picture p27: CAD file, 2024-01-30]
Step_models/machine/prowadnica.stp
300.0 x 50.0 x 52.0 mm
motor_nema17
sprzeglo
mocowanie_nema
stopka

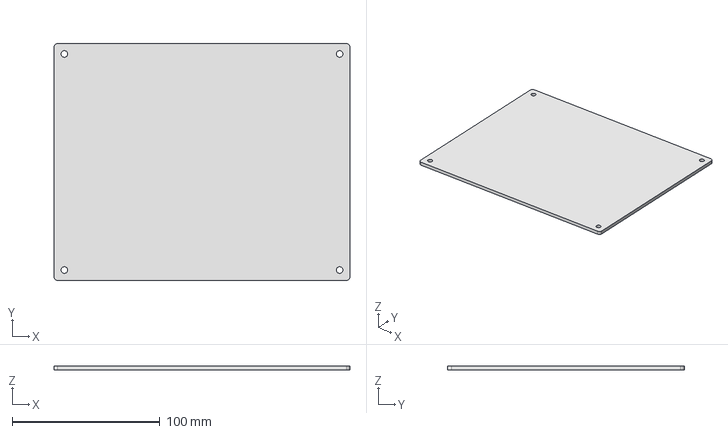
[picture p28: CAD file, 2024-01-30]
Step_models/electrical_components_enclosure/pokrywa.stp
200.0 x 160.0 x 3.00 mm

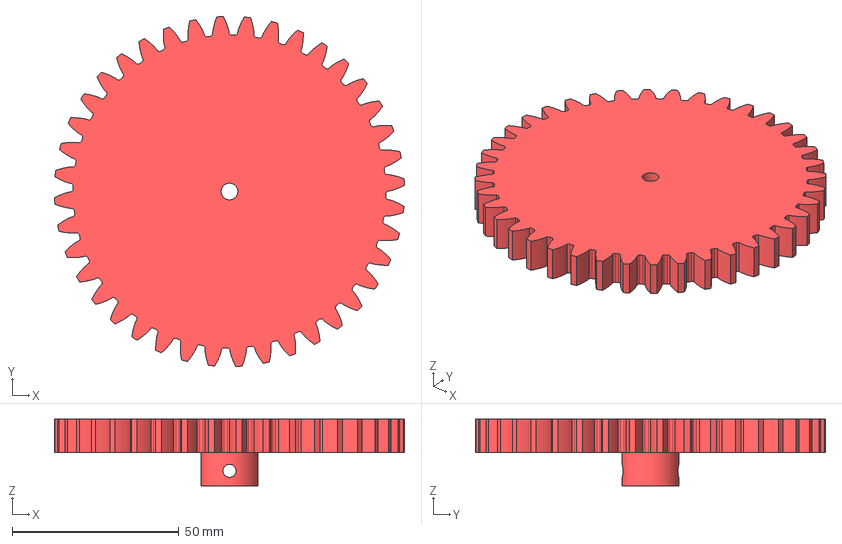
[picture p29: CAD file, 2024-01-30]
Step_models/machine/kolo zebate.stp
104.9 x 104.9 x 20.0 mm

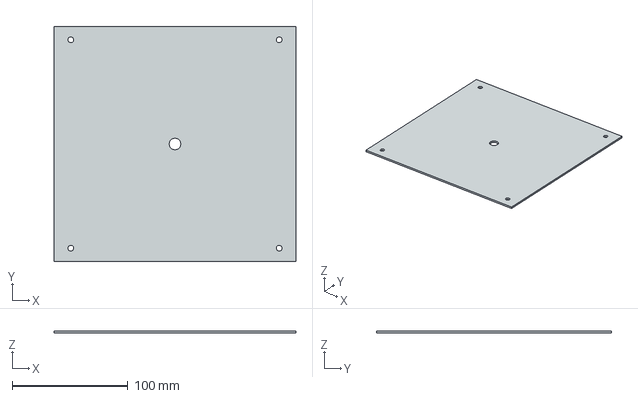
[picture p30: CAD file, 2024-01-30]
Step_models/machine/pokrywa podstawy.stp
209.0 x 203.0 x 2.00 mm

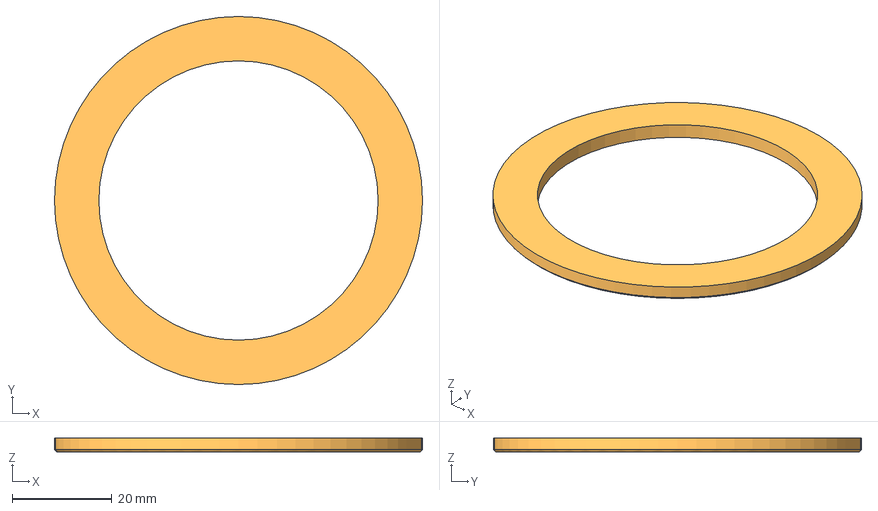
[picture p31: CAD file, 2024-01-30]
Step_models/machine/podkladka pod lozysko.stp
73.8 x 73.8 x 2.90 mm

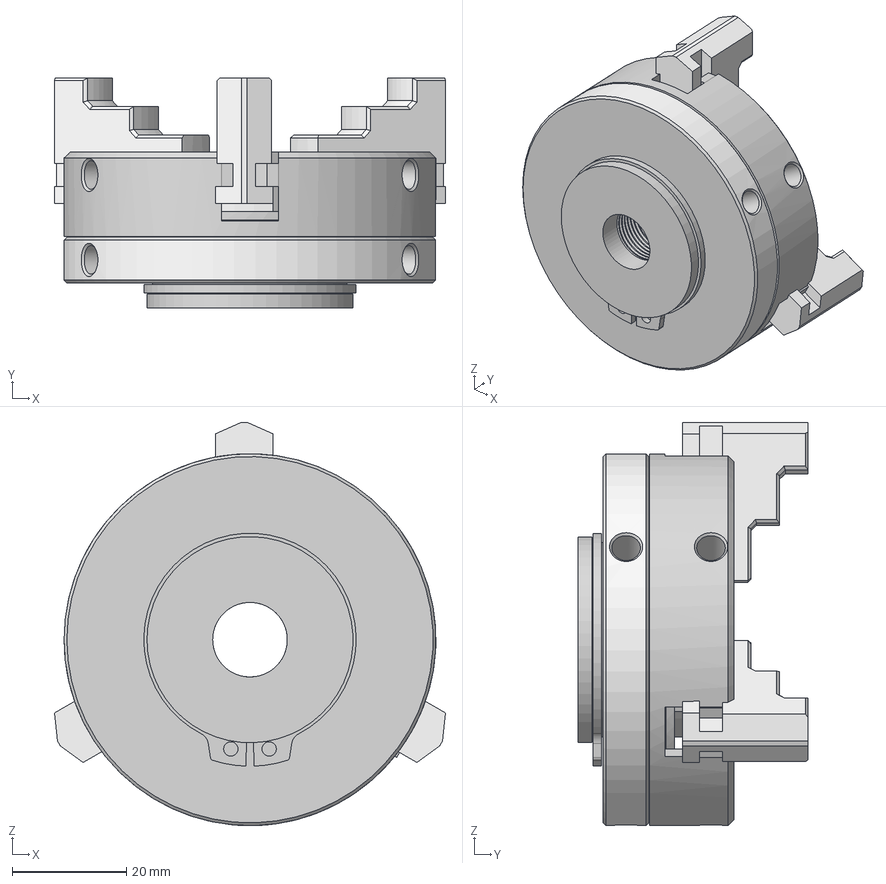
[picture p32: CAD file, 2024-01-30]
Step_models/machine/uchwyt trojszczekowy.stp
68.3 x 40.3 x 70.5 mm
Chuck
Jaw_1
base
Jaw_3
Jaw_2
98541A143_External Retaining Ring

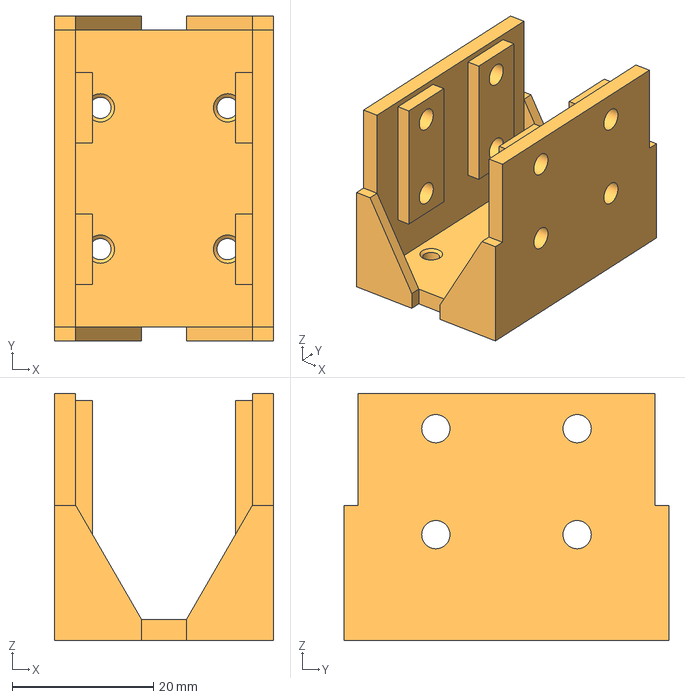
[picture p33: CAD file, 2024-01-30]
Step_models/machine/mocowanie ramienia.stp
31.0 x 46.0 x 35.0 mm

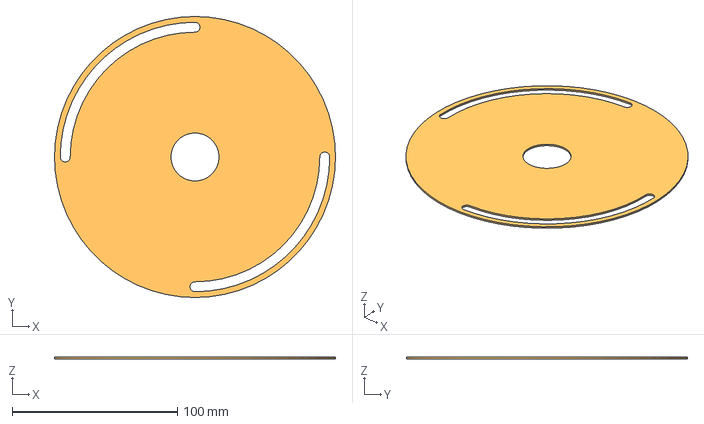
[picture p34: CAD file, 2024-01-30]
Step_models/machine/plytka pod anode.stp
170.0 x 170.0 x 1.00 mm

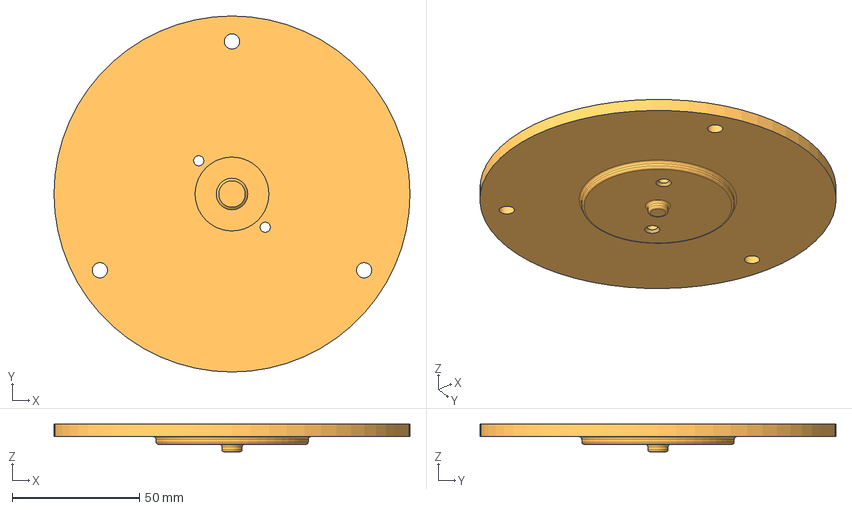
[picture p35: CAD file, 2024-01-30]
Step_models/machine/podstawa_lozyskowa_2.stp
140.0 x 140.0 x 11.0 mm

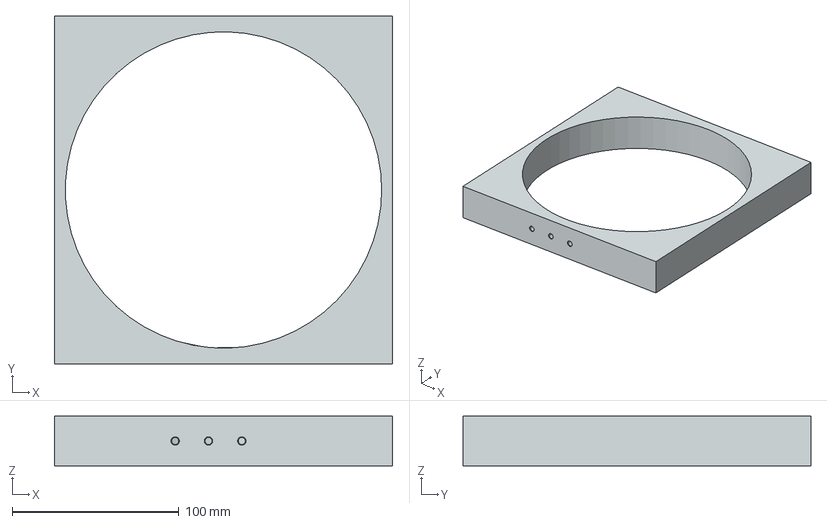
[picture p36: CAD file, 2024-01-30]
Step_models/machine/Podstawa.stp
203.0 x 209.0 x 30.0 mm

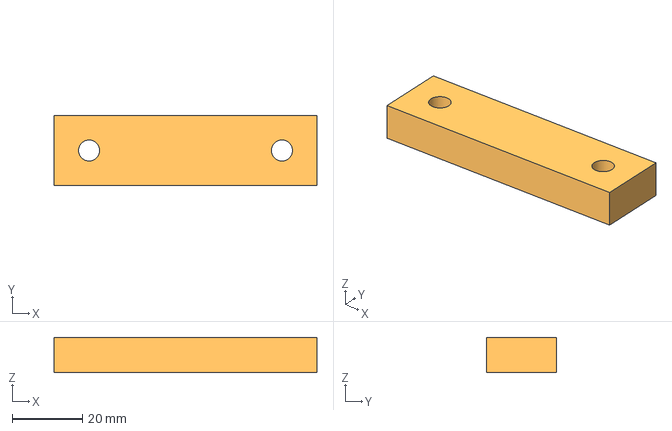
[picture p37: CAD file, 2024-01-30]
Step_models/machine/zacisk wewnetrzny.stp
75.0 x 20.0 x 10.0 mm

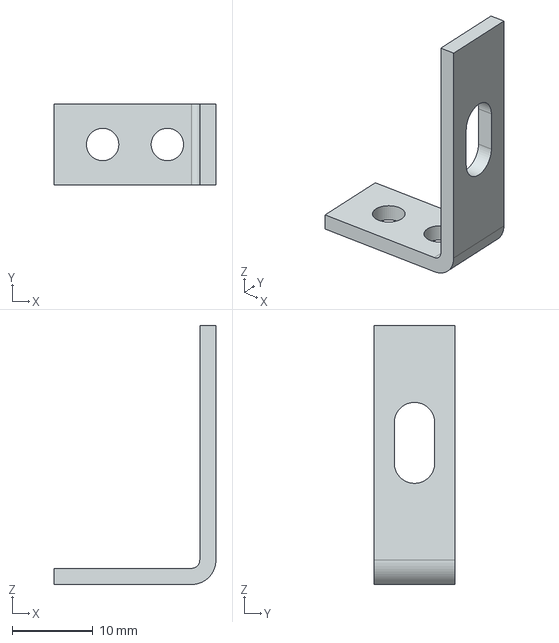
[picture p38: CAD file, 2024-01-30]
Step_models/machine/katownik.stp
20.0 x 10.0 x 32.0 mm

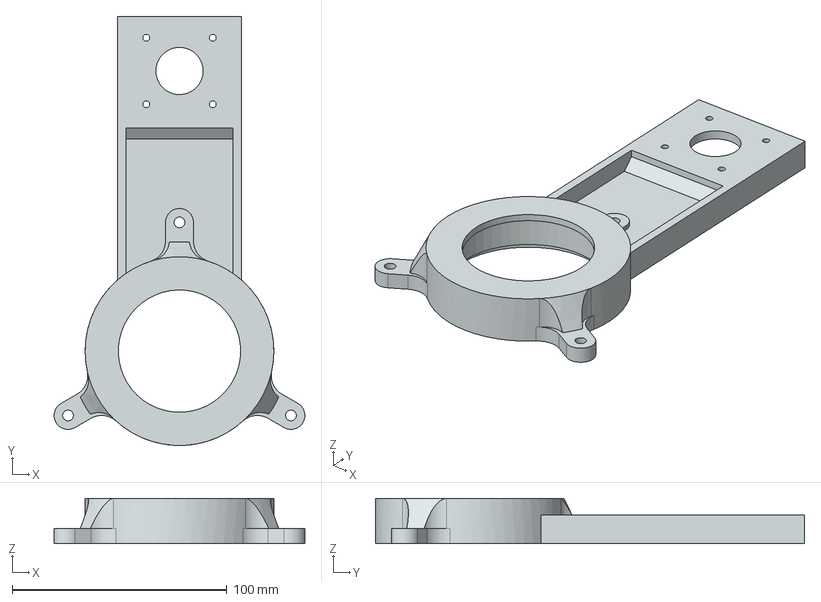
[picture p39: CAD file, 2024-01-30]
Step_models/machine/podstawa_lozyskowa.stp
116.9 x 200.0 x 21.0 mm

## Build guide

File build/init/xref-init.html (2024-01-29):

# modulegraph cross reference for init.py, pyi_rth_inspect.py, pyi_rth_pkgutil.py, pyi_rth_pyqt5.py

init.py Script

imports: PyQt5.QtCore • PyQt5.QtWidgets • PyQt5.uic • _collections_abc • _weakrefset • abc • codecs • collections • collections.abc • copyreg • encodings • encodings.aliases • encodings.ascii • encodings.base64_codec • encodings.big5 • encodings.big5hkscs • encodings.bz2_codec • encodings.charmap • encodings.cp037 • encodings.cp1006 • encodings.cp1026 • encodings.cp1125 • encodings.cp1140 • encodings.cp1250 • encodings.cp1251 • encodings.cp1252 • encodings.cp1253 • encodings.cp1254 • encodings.cp1255 • encodings.cp1256 • encodings.cp1257 • encodings.cp1258 • encodings.cp273 • encodings.cp424 • encodings.cp437 • encodings.cp500 • encodings.cp720 • encodings.cp737 • encodings.cp775 • encodings.cp850 • encodings.cp852 • encodings.cp855 • encodings.cp856 • encodings.cp857 • encodings.cp858 • encodings.cp860 • encodings.cp861 • encodings.cp862 • encodings.cp863 • encodings.cp864 • encodings.cp865 • encodings.cp866 • encodings.cp869 • encodings.cp874 • encodings.cp875 • encodings.cp932 • encodings.cp949 • encodings.cp950 • encodings.euc_jis_2004 • encodings.euc_jisx0213 • encodings.euc_jp • encodings.euc_kr • encodings.gb18030 • encodings.gb2312 • encodings.gbk • encodings.hex_codec • encodings.hp_roman8 • encodings.hz • encodings.idna • encodings.iso2022_jp • encodings.iso2022_jp_1 • encodings.iso2022_jp_2 • encodings.iso2022_jp_2004 • encodings.iso2022_jp_3 • encodings.iso2022_jp_ext • encodings.iso2022_kr • encodings.iso8859_1 • encodings.iso8859_10 • encodings.iso8859_11 • encodings.iso8859_13 • encodings.iso8859_14 • encodings.iso8859_15 • encodings.iso8859_16 • encodings.iso8859_2 • encodings.iso8859_3 • encodings.iso8859_4 • encodings.iso8859_5 • encodings.iso8859_6 • encodings.iso8859_7 • encodings.iso8859_8 • encodings.iso8859_9 • encodings.johab • encodings.koi8_r • encodings.koi8_t • encodings.koi8_u • encodings.kz1048 • encodings.latin_1 • encodings.mac_arabic • encodings.mac_croatian • encodings.mac_cyrillic • encodings.mac_farsi • encodings.mac_greek • encodings.mac_iceland • encodings.mac_latin2 • encodings.mac_roman • encodings.mac_romanian • encodings.mac_turkish • encodings.mbcs • encodings.oem • encodings.palmos • encodings.ptcp154 • encodings.punycode • encodings.quopri_codec • encodings.raw_unicode_escape • encodings.rot_13 • encodings.shift_jis • encodings.shift_jis_2004 • encodings.shift_jisx0213 • encodings.tis_620 • encodings.undefined • encodings.unicode_escape • encodings.utf_16 • encodings.utf_16_be • encodings.utf_16_le • encodings.utf_32 • encodings.utf_32_be • encodings.utf_32_le • encodings.utf_7 • encodings.utf_8 • encodings.utf_8_sig • encodings.uu_codec • encodings.zlib_codec • enum • functools • genericpath • heapq • io • keyword • linecache • locale • ntpath • operator • os • posixpath • pyi_rth_inspect.py • pyi_rth_pkgutil.py • pyi_rth_pyqt5.py • re • reprlib • serial • serial.tools.list_ports • sre_compile • sre_constants • sre_parse • stat • sys • time • traceback • types • warnings • weakref

pyi_rth_inspect.py Script

imports: inspect • os • sys

imported by: init.py

pyi_rth_pkgutil.py Script

imports: os • pkgutil • pyimod02_importers • sys

imported by: init.py

pyi_rth_pyqt5.py Script

imports: os • sys

imported by: init.py

'System.IO' MissingModule

imported by: serial.serialcli

'org.python' MissingModule

imported by: copy • xml.sax

PyQt5 Package

imports: PyQt5.QtGui • PyQt5.sip • os • pkgutil • sys

imported by: PyQt5.QtCore • PyQt5.QtGui • PyQt5.QtWidgets • PyQt5.sip • PyQt5.uic • PyQt5.uic.Loader.loader • PyQt5.uic.Loader.qobjectcreator

PyQt5.QtCore C:\Users\daron\AppData\Local\Programs\Python\Python310\lib\site-packages\PyQt5\QtCore.pyd

imports: PyQt5

imported by: PyQt5.QtGui • PyQt5.QtWidgets • PyQt5.uic • PyQt5.uic.Loader.loader • init.py

PyQt5.QtGui C:\Users\daron\AppData\Local\Programs\Python\Python310\lib\site-packages\PyQt5\QtGui.pyd

imports: PyQt5 • PyQt5.QtCore

imported by: PyQt5 • PyQt5.QtWidgets • PyQt5.uic.Loader.loader • PyQt5.uic.Loader.qobjectcreator

PyQt5.QtWidgets C:\Users\daron\AppData\Local\Programs\Python\Python310\lib\site-packages\PyQt5\QtWidgets.pyd

imports: PyQt5 • PyQt5.QtCore • PyQt5.QtGui

imported by: PyQt5.uic • PyQt5.uic.Loader.loader • PyQt5.uic.Loader.qobjectcreator • init.py

PyQt5.sip C:\Users\daron\AppData\Local\Programs\Python\Python310\lib\site-packages\PyQt5\sip.cp310-win_amd64.pyd

imports: PyQt5

imported by: PyQt5

PyQt5.uic Package

imports: PyQt5 • PyQt5.QtCore • PyQt5.QtWidgets • PyQt5.uic.Compiler • PyQt5.uic.Compiler.compiler • PyQt5.uic.Compiler.indenter • PyQt5.uic.Loader.loader • PyQt5.uic.objcreator • PyQt5.uic.port_v2.string_io • PyQt5.uic.port_v3.string_io • os • sys

imported by: PyQt5.uic.Compiler • PyQt5.uic.Loader • PyQt5.uic.exceptions • PyQt5.uic.icon_cache • PyQt5.uic.objcreator • PyQt5.uic.port_v2 • PyQt5.uic.port_v3 • PyQt5.uic.properties • PyQt5.uic.uiparser • init.py

PyQt5.uic.Compiler Package

imports: PyQt5.uic • PyQt5.uic.Compiler • PyQt5.uic.Compiler.compiler • PyQt5.uic.Compiler.indenter • PyQt5.uic.Compiler.qtproxies

imported by: PyQt5.uic • PyQt5.uic.Compiler • PyQt5.uic.Compiler.compiler • PyQt5.uic.Compiler.indenter • PyQt5.uic.Compiler.misc • PyQt5.uic.Compiler.proxy_metaclass • PyQt5.uic.Compiler.qobjectcreator • PyQt5.uic.Compiler.qtproxies

PyQt5.uic.Compiler.compiler SourceModule

imports: PyQt5.uic.Compiler • PyQt5.uic.Compiler.indenter • PyQt5.uic.Compiler.qobjectcreator • PyQt5.uic.Compiler.qtproxies • PyQt5.uic.properties • PyQt5.uic.uiparser • sys

imported by: PyQt5.uic • PyQt5.uic.Compiler

PyQt5.uic.Compiler.indenter SourceModule

imports: PyQt5.uic.Compiler

imported by: PyQt5.uic • PyQt5.uic.Compiler • PyQt5.uic.Compiler.compiler • PyQt5.uic.Compiler.qobjectcreator • PyQt5.uic.Compiler.qtproxies

PyQt5.uic.Compiler.misc SourceModule

imports: PyQt5.uic.Compiler

imported by: PyQt5.uic.Compiler.proxy_metaclass • PyQt5.uic.Compiler.qtproxies

PyQt5.uic.Compiler.proxy_metaclass SourceModule

imports: PyQt5.uic.Compiler • PyQt5.uic.Compiler.misc • PyQt5.uic.Compiler.qtproxies

imported by: PyQt5.uic.port_v2.proxy_base • PyQt5.uic.port_v3.proxy_base

PyQt5.uic.Compiler.qobjectcreator SourceModule

imports: PyQt5.uic.Compiler • PyQt5.uic.Compiler.indenter • PyQt5.uic.Compiler.qtproxies • PyQt5.uic.port_v2.as_string • PyQt5.uic.port_v3.as_string • logging • sys

imported by: PyQt5.uic.Compiler.compiler

PyQt5.uic.Compiler.qtproxies SourceModule

imports: PyQt5.uic.Compiler • PyQt5.uic.Compiler.indenter • PyQt5.uic.Compiler.misc • PyQt5.uic.port_v2.as_string • PyQt5.uic.port_v2.proxy_base • PyQt5.uic.port_v3.as_string • PyQt5.uic.port_v3.proxy_base • re • sys

imported by: PyQt5.uic.Compiler • PyQt5.uic.Compiler.compiler • PyQt5.uic.Compiler.proxy_metaclass • PyQt5.uic.Compiler.qobjectcreator

PyQt5.uic.Loader Package

imports: PyQt5.uic

imported by: PyQt5.uic.Loader.loader • PyQt5.uic.Loader.qobjectcreator

PyQt5.uic.Loader.loader SourceModule

imports: PyQt5 • PyQt5.QtCore • PyQt5.QtGui • PyQt5.QtWidgets • PyQt5.uic.Loader • PyQt5.uic.Loader.qobjectcreator • PyQt5.uic.uiparser

imported by: PyQt5.uic

PyQt5.uic.Loader.qobjectcreator SourceModule

imports: PyQt5 • PyQt5.QtGui • PyQt5.QtWidgets • PyQt5.uic.Loader • sys

imported by: PyQt5.uic.Loader.loader

PyQt5.uic.exceptions SourceModule

imports: PyQt5.uic

imported by: PyQt5.uic.objcreator • PyQt5.uic.properties

PyQt5.uic.icon_cache SourceModule

imports: PyQt5.uic • ntpath

imported by: PyQt5.uic.properties

PyQt5.uic.objcreator SourceModule

imports: PyQt5.uic • PyQt5.uic.exceptions • ntpath

imported by: PyQt5.uic • PyQt5.uic.uiparser

PyQt5.uic.port_v2 Package

imports: PyQt5.uic

imported by: PyQt5.uic.port_v2.as_string • PyQt5.uic.port_v2.proxy_base • PyQt5.uic.port_v2.string_io

PyQt5.uic.port_v2.as_string SourceModule

imports: PyQt5.uic.port_v2 • re

imported by: PyQt5.uic.Compiler.qobjectcreator • PyQt5.uic.Compiler.qtproxies

PyQt5.uic.port_v2.proxy_base SourceModule

imports: PyQt5.uic.Compiler.proxy_metaclass • PyQt5.uic.port_v2

imported by: PyQt5.uic.Compiler.qtproxies

PyQt5.uic.port_v2.string_io SourceModule

imports: PyQt5.uic.port_v2 • StringIO • cStringIO

imported by: PyQt5.uic

PyQt5.uic.port_v3 Package

imports: PyQt5.uic

imported by: PyQt5.uic.port_v3.as_string • PyQt5.uic.port_v3.ascii_upper • PyQt5.uic.port_v3.proxy_base • PyQt5.uic.port_v3.string_io

PyQt5.uic.port_v3.as_string SourceModule

imports: PyQt5.uic.port_v3 • re

imported by: PyQt5.uic.Compiler.qobjectcreator • PyQt5.uic.Compiler.qtproxies

PyQt5.uic.port_v3.ascii_upper SourceModule

imports: PyQt5.uic.port_v3

imported by: PyQt5.uic.properties

PyQt5.uic.port_v3.proxy_base SourceModule

imports: PyQt5.uic.Compiler.proxy_metaclass • PyQt5.uic.port_v3

imported by: PyQt5.uic.Compiler.qtproxies

PyQt5.uic.port_v3.string_io SourceModule

imports: PyQt5.uic.port_v3 • io

imported by: PyQt5.uic

PyQt5.uic.properties SourceModule

imports: PyQt5.uic • PyQt5.uic.exceptions • PyQt5.uic.icon_cache • PyQt5.uic.port_v3.ascii_upper • logging • ntpath • port_v2 • sys

imported by: PyQt5.uic.Compiler.compiler • PyQt5.uic.uiparser

PyQt5.uic.uiparser SourceModule

imports: PyQt5.uic • PyQt5.uic.objcreator • PyQt5.uic.properties • logging • os • re • sys • xml.etree.ElementTree

imported by: PyQt5.uic.Compiler.compiler • PyQt5.uic.Loader.loader

StringIO MissingModule

imported by: PyQt5.uic.port_v2.string_io

System MissingModule

imported by: serial.serialcli

_abc (builtin module)

imported by: abc

_ast (builtin module)

imported by: ast

_bisect (builtin module)

imported by: bisect

_blake2 (builtin module)

imported by: hashlib

_bz2 C:\Users\daron\AppData\Local\Programs\Python\Python310\DLLs\_bz2.pyd

imported by: bz2

_codecs (builtin module)

imported by: codecs

_codecs_cn (builtin module)

imported by: encodings.gb18030 • encodings.gb2312 • encodings.gbk • encodings.hz

_codecs_hk (builtin module)

imported by: encodings.big5hkscs

_codecs_iso2022 (builtin module)

imported by: encodings.iso2022_jp • encodings.iso2022_jp_1 • encodings.iso2022_jp_2 • encodings.iso2022_jp_2004 • encodings.iso2022_jp_3 • encodings.iso2022_jp_ext • encodings.iso2022_kr

_codecs_jp (builtin module)

imported by: encodings.cp932 • encodings.euc_jis_2004 • encodings.euc_jisx0213 • encodings.euc_jp • encodings.shift_jis • encodings.shift_jis_2004 • encodings.shift_jisx0213

_codecs_kr (builtin module)

imported by: encodings.cp949 • encodings.euc_kr • encodings.johab

_codecs_tw (builtin module)

imported by: encodings.big5 • encodings.cp950

_collections (builtin module)

imported by: collections • threading

_collections_abc SourceModule

imports: abc • sys

imported by: collections • collections.abc • contextlib • init.py • locale • os • pathlib • random • types • weakref

_compat_pickle SourceModule

imported by: _pickle • pickle

_compression SourceModule

imports: io • sys

imported by: bz2 • gzip • lzma

_contextvars (builtin module)

imported by: contextvars

_csv (builtin module)

imported by: csv

_ctypes C:\Users\daron\AppData\Local\Programs\Python\Python310\DLLs\_ctypes.pyd

imported by: ctypes • ctypes.macholib.dyld

_datetime (builtin module)

imports: _strptime • time

imported by: datetime

_decimal C:\Users\daron\AppData\Local\Programs\Python\Python310\DLLs\_decimal.pyd

imported by: decimal

_elementtree C:\Users\daron\AppData\Local\Programs\Python\Python310\DLLs\_elementtree.pyd

imports: pyexpat • xml.etree.ElementInclude • xml.etree.ElementPath • xml.etree.ElementTree • xml.etree.cElementTree

imported by: xml.etree.ElementTree

_frozen_importlib ExcludedModule

imported by: importlib • importlib.abc • zipimport

_frozen_importlib_external MissingModule

imported by: importlib • importlib._bootstrap • importlib.abc • zipimport

_functools (builtin module)

imported by: functools

_hashlib C:\Users\daron\AppData\Local\Programs\Python\Python310\DLLs\_hashlib.pyd

imported by: hashlib

_heapq (builtin module)

imported by: heapq

_imp (builtin module)

imported by: importlib • importlib._bootstrap_external • importlib.util • zipimport

_io (builtin module)

imported by: importlib._bootstrap_external • io • zipimport

_locale (builtin module)

imported by: locale • re

_lzma C:\Users\daron\AppData\Local\Programs\Python\Python310\DLLs\_lzma.pyd

imported by: lzma

_md5 (builtin module)

imported by: hashlib

_multibytecodec (builtin module)

imported by: encodings.big5 • encodings.big5hkscs • encodings.cp932 • encodings.cp949 • encodings.cp950 • encodings.euc_jis_2004 • encodings.euc_jisx0213 • encodings.euc_jp • encodings.euc_kr • encodings.gb18030 • encodings.gb2312 • encodings.gbk • encodings.hz • encodings.iso2022_jp • encodings.iso2022_jp_1 • encodings.iso2022_jp_2 • encodings.iso2022_jp_2004 • encodings.iso2022_jp_3 • encodings.iso2022_jp_ext • encodings.iso2022_kr • encodings.johab • encodings.shift_jis • encodings.shift_jis_2004 • encodings.shift_jisx0213

_opcode (builtin module)

imported by: opcode

_operator (builtin module)

imported by: operator

_pickle (builtin module)

imports: _compat_pickle • codecs • copyreg

imported by: pickle

_posixsubprocess MissingModule

imports: gc

imported by: subprocess

_py_abc SourceModule

imports: _weakrefset

imported by: abc

_pydecimal SourceModule

imports: collections • contextvars • itertools • locale • math • numbers • re • sys

imported by: decimal

_random (builtin module)

imported by: random

_scproxy MissingModule

imported by: urllib.request

_sha1 (builtin module)

imported by: hashlib

_sha256 (builtin module)

imported by: hashlib

_sha3 (builtin module)

imported by: hashlib

_sha512 (builtin module)

imported by: hashlib • random

_signal (builtin module)

imported by: signal

_socket C:\Users\daron\AppData\Local\Programs\Python\Python310\DLLs\_socket.pyd

imported by: socket

_sre (builtin module)

imports: copy • re

imported by: sre_compile • sre_constants

_ssl C:\Users\daron\AppData\Local\Programs\Python\Python310\DLLs\_ssl.pyd

imports: socket

imported by: ssl

_stat (builtin module)

imported by: stat

_statistics (builtin module)

imported by: statistics

_string (builtin module)

imported by: string

_strptime SourceModule

imports: _thread • calendar • datetime • locale • re • time

imported by: _datetime • datetime • time

_struct (builtin module)

imported by: struct

_thread (builtin module)

imported by: _strptime • dataclasses • functools • reprlib • tempfile • threading

_threading_local SourceModule

imports: contextlib • threading • weakref

imported by: threading

_tracemalloc (builtin module)

imported by: tracemalloc

_warnings (builtin module)

imported by: importlib._bootstrap_external • warnings • zipimport

_weakref (builtin module)

imported by: _weakrefset • collections • weakref • xml.sax.expatreader

_weakrefset SourceModule

imports: _weakref • types

imported by: _py_abc • init.py • threading • weakref

_winapi (builtin module)

imported by: encodings • mimetypes • subprocess

abc SourceModule

imports: _abc • _py_abc

imported by: _collections_abc • contextlib • dataclasses • email._policybase • functools • importlib._abc • importlib.abc • importlib.metadata • init.py • inspect • io • numbers • os • selectors • typing

argparse SourceModule

imports: copy • gettext • os • re • shutil • sys • textwrap • warnings

imported by: ast • calendar • dis • gzip • inspect • py_compile • serial.tools.list_ports • tarfile • tokenize • zipfile

array (builtin module)

imported by: serial.serialposix • serial.serialutil • socket

ast SourceModule

imports: _ast • argparse • collections • contextlib • enum • inspect • sys • warnings

imported by: inspect

atexit (builtin module)

imported by: logging • weakref

base64 SourceModule

imports: binascii • getopt • re • struct • sys

imported by: email._encoded_words • email.base64mime • email.encoders • encodings.base64_codec • ssl • urllib.request

binascii (builtin module)

imported by: base64 • email._encoded_words • email.base64mime • email.contentmanager • email.header • encodings.hex_codec • encodings.uu_codec • quopri • uu • zipfile

bisect SourceModule

imports: _bisect

imported by: random • statistics • urllib.request

builtins (builtin module)

imported by: bz2 • codecs • dataclasses • gettext • gzip • inspect • locale • lzma • operator • reprlib • subprocess • tarfile • tokenize • warnings

bz2 SourceModule

imports: _bz2 • _compression • builtins • io • os

imported by: encodings.bz2_codec • shutil • tarfile • zipfile

cStringIO MissingModule

imports: copy_reg

imported by: PyQt5.uic.port_v2.string_io

calendar SourceModule

imports: argparse • datetime • itertools • locale • sys

imported by: _strptime • email._parseaddr • http.cookiejar • ssl

codecs SourceModule

imports: _codecs • builtins • encodings • sys

imported by: _pickle • encodings • encodings.ascii • encodings.base64_codec • encodings.big5 • encodings.big5hkscs • encodings.bz2_codec • encodings.charmap • encodings.cp037 • encodings.cp1006 • encodings.cp1026 • encodings.cp1125 • encodings.cp1140 • encodings.cp1250 • encodings.cp1251 • encodings.cp1252 • encodings.cp1253 • encodings.cp1254 • encodings.cp1255 • encodings.cp1256 • encodings.cp1257 • encodings.cp1258 • encodings.cp273 • encodings.cp424 • encodings.cp437 • encodings.cp500 • encodings.cp720 • encodings.cp737 • encodings.cp775 • encodings.cp850 • encodings.cp852 • encodings.cp855 • encodings.cp856 • encodings.cp857 • encodings.cp858 • encodings.cp860 • encodings.cp861 • encodings.cp862 • encodings.cp863 • encodings.cp864 • encodings.cp865 • encodings.cp866 • encodings.cp869 • encodings.cp874 • encodings.cp875 • encodings.cp932 • encodings.cp949 • encodings.cp950 • encodings.euc_jis_2004 • encodings.euc_jisx0213 • encodings.euc_jp • encodings.euc_kr • encodings.gb18030 • encodings.gb2312 • encodings.gbk • encodings.hex_codec • encodings.hp_roman8 • encodings.hz • encodings.idna • encodings.iso2022_jp • encodings.iso2022_jp_1 • encodings.iso2022_jp_2 • encodings.iso2022_jp_2004 • encodings.iso2022_jp_3 • encodings.iso2022_jp_ext • encodings.iso2022_kr • encodings.iso8859_1 • encodings.iso8859_10 • encodings.iso8859_11 • encodings.iso8859_13 • encodings.iso8859_14 • encodings.iso8859_15 • encodings.iso8859_16 • encodings.iso8859_2 • encodings.iso8859_3 • encodings.iso8859_4 • encodings.iso8859_5 • encodings.iso8859_6 • encodings.iso8859_7 • encodings.iso8859_8 • encodings.iso8859_9 • encodings.johab • encodings.koi8_r • encodings.koi8_t • encodings.koi8_u • encodings.kz1048 • encodings.latin_1 • encodings.mac_arabic • encodings.mac_croatian • encodings.mac_cyrillic • encodings.mac_farsi • encodings.mac_greek • encodings.mac_iceland • encodings.mac_latin2 • encodings.mac_roman • encodings.mac_romanian • encodings.mac_turkish • encodings.mbcs • encodings.oem • encodings.palmos • encodings.ptcp154 • encodings.punycode • encodings.quopri_codec • encodings.raw_unicode_escape • encodings.rot_13 • encodings.shift_jis • encodings.shift_jis_2004 • encodings.shift_jisx0213 • encodings.tis_620 • encodings.undefined • encodings.unicode_escape • encodings.utf_16 • encodings.utf_16_be • encodings.utf_16_le • encodings.utf_32 • encodings.utf_32_be • encodings.utf_32_le • encodings.utf_7 • encodings.utf_8 • encodings.utf_8_sig • encodings.uu_codec • encodings.zlib_codec • init.py • pickle • tokenize • xml.sax.saxutils

collections Package

imports: _collections • _collections_abc • _weakref • copy • heapq • itertools • keyword • operator • reprlib • sys

imported by: _pydecimal • ast • collections.abc • contextlib • dis • email.feedparser • functools • importlib.metadata • importlib.metadata._collections • importlib.readers • init.py • inspect • pkgutil • pprint • selectors • shlex • shutil • ssl • statistics • string • threading • tokenize • traceback • typing • urllib.parse • xml.etree.ElementTree

collections.abc SourceModule

imports: _collections_abc • collections

imported by: http.client • init.py • inspect • logging • selectors • tracemalloc • typing • xml.etree.ElementTree

contextlib SourceModule

imports: _collections_abc • abc • collections • functools • sys • types

imported by: _threading_local • ast • getpass • glob • importlib.metadata • importlib.util • subprocess • typing • urllib.request • xml.etree.ElementTree • zipfile

contextvars SourceModule

imports: _contextvars

imported by: _pydecimal

copy SourceModule

imports: 'org.python' • copyreg • types • weakref

imported by: _sre • argparse • collections • dataclasses • email.generator • gettext • http.cookiejar • tarfile • weakref • xml.etree.ElementInclude

copy_reg MissingModule

imported by: cStringIO

copyreg SourceModule

imports: functools • operator

imported by: _pickle • copy • init.py • pickle • re

csv SourceModule

imports: _csv • io • re

imported by: importlib.metadata

ctypes Package

imports: _ctypes • ctypes._endian • nt • os • struct • sys • types

imported by: ctypes._aix • ctypes._endian • ctypes.macholib • ctypes.util • ctypes.wintypes • serial.serialwin32 • serial.tools.list_ports_osx • serial.tools.list_ports_windows • serial.win32

ctypes._aix SourceModule

imports: ctypes • os • re • subprocess • sys

imported by: ctypes.util

ctypes._endian SourceModule

imports: ctypes • sys

imported by: ctypes

ctypes.macholib Package

imports: ctypes

imported by: ctypes.macholib.dyld • ctypes.macholib.dylib • ctypes.macholib.framework

ctypes.macholib.dyld SourceModule

imports: _ctypes • ctypes.macholib • ctypes.macholib.dylib • ctypes.macholib.framework • itertools • os

imported by: ctypes.util

ctypes.macholib.dylib SourceModule

imports: ctypes.macholib • re

imported by: ctypes.macholib.dyld

ctypes.macholib.framework SourceModule

imports: ctypes.macholib • re

imported by: ctypes.macholib.dyld

ctypes.util SourceModule

imports: ctypes • ctypes._aix • ctypes.macholib.dyld • importlib.machinery • os • re • shutil • struct • subprocess • sys • tempfile

imported by: serial.tools.list_ports_osx

ctypes.wintypes SourceModule

imports: ctypes

imported by: serial.tools.list_ports_windows • serial.win32

dataclasses SourceModule

imports: _thread • abc • builtins • copy • functools • inspect • keyword • re • sys • types

imported by: pprint

datetime SourceModule

imports: _datetime • _strptime • math • operator • sys • time

imported by: _strptime • calendar • email.utils • http.cookiejar

decimal SourceModule

imports: _decimal • _pydecimal

imported by: fractions • statistics

dis SourceModule

imports: argparse • collections • io • opcode • sys • types

imported by: inspect

email Package

imports: email._header_value_parser • email.charset • email.errors • email.header • email.parser

imported by: email._encoded_words • email._header_value_parser • email._parseaddr • email._policybase • email.base64mime • email.charset • email.contentmanager • email.encoders • email.errors • email.feedparser • email.generator • email.header • email.headerregistry • email.iterators • email.message • email.parser • email.policy • email.quoprimime • email.utils • importlib.metadata • urllib.request

email._encoded_words SourceModule

imports: base64 • binascii • email • email.errors • functools • re • string

imported by: email._header_value_parser • email.message

email._header_value_parser SourceModule

imports: email • email._encoded_words • email.errors • email.utils • operator • re • string • sys • urllib

imported by: email • email.headerregistry

email._parseaddr SourceModule

imports: calendar • email • time

imported by: email.utils

email._policybase SourceModule

imports: abc • email • email.charset • email.header • email.utils

imported by: email.feedparser • email.message • email.parser • email.policy

email.base64mime SourceModule

imports: base64 • binascii • email

imported by: email.charset • email.header

email.charset SourceModule

imports: email • email.base64mime • email.encoders • email.errors • email.quoprimime • functools

imported by: email • email._policybase • email.contentmanager • email.header • email.message • email.utils

email.contentmanager SourceModule

imports: binascii • email • email.charset • email.errors • email.message • email.quoprimime

imported by: email.policy

email.encoders SourceModule

imports: base64 • email • quopri

imported by: email.charset

email.errors SourceModule

imports: email

imported by: email • email._encoded_words • email._header_value_parser • email.charset • email.contentmanager • email.feedparser • email.header • email.headerregistry • email.message

email.feedparser SourceModule

imports: collections • email • email._policybase • email.errors • email.message • io • re

imported by: email.parser

email.generator SourceModule

imports: copy • email • email.utils • io • random • re • sys • time

imported by: email.message

email.header SourceModule

imports: binascii • email • email.base64mime • email.charset • email.errors • email.quoprimime • re

imported by: email • email._policybase

email.headerregistry SourceModule

imports: email • email._header_value_parser • email.errors • email.utils • types

imported by: email.policy

email.iterators SourceModule

imports: email • io • sys

imported by: email.message

email.message SourceModule

imports: email • email._encoded_words • email._policybase • email.charset • email.errors • email.generator • email.iterators • email.policy • email.utils • io • quopri • re • uu

imported by: email.contentmanager • email.feedparser • email.policy • http.client • importlib.metadata._adapters

email.parser SourceModule

imports: email • email._policybase • email.feedparser • io

imported by: email • http.client

email.policy SourceModule

imports: email • email._policybase • email.contentmanager • email.headerregistry • email.message • email.utils • re • sys

imported by: email.message

email.quoprimime SourceModule

imports: email • re • string

imported by: email.charset • email.contentmanager • email.header

email.utils SourceModule

imports: datetime • email • email._parseaddr • email.charset • os • random • re • socket • time • urllib.parse

imported by: email._header_value_parser • email._policybase • email.generator • email.headerregistry • email.message • email.policy • urllib.request

encodings Package

imports: _winapi • codecs • encodings • encodings.aliases • encodings.ascii • encodings.base64_codec • encodings.big5 • encodings.big5hkscs • encodings.bz2_codec • encodings.charmap • encodings.cp037 • encodings.cp1006 • encodings.cp1026 • encodings.cp1125 • encodings.cp1140 • encodings.cp1250 • encodings.cp1251 • encodings.cp1252 • encodings.cp1253 • encodings.cp1254 • encodings.cp1255 • encodings.cp1256 • encodings.cp1257 • encodings.cp1258 • encodings.cp273 • encodings.cp424 • encodings.cp437 • encodings.cp500 • encodings.cp720 • encodings.cp737 • encodings.cp775 • encodings.cp850 • encodings.cp852 • encodings.cp855 • encodings.cp856 • encodings.cp857 • encodings.cp858 • encodings.cp860 • encodings.cp861 • encodings.cp862 • encodings.cp863 • encodings.cp864 • encodings.cp865 • encodings.cp866 • encodings.cp869 • encodings.cp874 • encodings.cp875 • encodings.cp932 • encodings.cp949 • encodings.cp950 • encodings.euc_jis_2004 • encodings.euc_jisx0213 • encodings.euc_jp • encodings.euc_kr • encodings.gb18030 • encodings.gb2312 • encodings.gbk • encodings.hex_codec • encodings.hp_roman8 • encodings.hz • encodings.idna • encodings.iso2022_jp • encodings.iso2022_jp_1 • encodings.iso2022_jp_2 • encodings.iso2022_jp_2004 • encodings.iso2022_jp_3 • encodings.iso2022_jp_ext • encodings.iso2022_kr • encodings.iso8859_1 • encodings.iso8859_10 • encodings.iso8859_11 • encodings.iso8859_13 • encodings.iso8859_14 • encodings.iso8859_15 • encodings.iso8859_16 • encodings.iso8859_2 • encodings.iso8859_3 • encodings.iso8859_4 • encodings.iso8859_5 • encodings.iso8859_6 • encodings.iso8859_7 • encodings.iso8859_8 • encodings.iso8859_9 • encodings.johab • encodings.koi8_r • encodings.koi8_t • encodings.koi8_u • encodings.kz1048 • encodings.latin_1 • encodings.mac_arabic • encodings.mac_croatian • encodings.mac_cyrillic • encodings.mac_farsi • encodings.mac_greek • encodings.mac_iceland • encodings.mac_latin2 • encodings.mac_roman • encodings.mac_romanian • encodings.mac_turkish • encodings.mbcs • encodings.oem • encodings.palmos • encodings.ptcp154 • encodings.punycode • encodings.quopri_codec • encodings.raw_unicode_escape • encodings.rot_13 • encodings.shift_jis • encodings.shift_jis_2004 • encodings.shift_jisx0213 • encodings.tis_620 • encodings.undefined • encodings.unicode_escape • encodings.utf_16 • encodings.utf_16_be • encodings.utf_16_le • encodings.utf_32 • encodings.utf_32_be • encodings.utf_32_le • encodings.utf_7 • encodings.utf_8 • encodings.utf_8_sig • encodings.uu_codec • encodings.zlib_codec • sys

imported by: codecs • encodings • encodings.aliases • encodings.ascii • encodings.base64_codec • encodings.big5 • encodings.big5hkscs • encodings.bz2_codec • encodings.charmap • encodings.cp037 • encodings.cp1006 • encodings.cp1026 • encodings.cp1125 • encodings.cp1140 • encodings.cp1250 • encodings.cp1251 • encodings.cp1252 • encodings.cp1253 • encodings.cp1254 • encodings.cp1255 • encodings.cp1256 • encodings.cp1257 • encodings.cp1258 • encodings.cp273 • encodings.cp424 • encodings.cp437 • encodings.cp500 • encodings.cp720 • encodings.cp737 • encodings.cp775 • encodings.cp850 • encodings.cp852 • encodings.cp855 • encodings.cp856 • encodings.cp857 • encodings.cp858 • encodings.cp860 • encodings.cp861 • encodings.cp862 • encodings.cp863 • encodings.cp864 • encodings.cp865 • encodings.cp866 • encodings.cp869 • encodings.cp874 • encodings.cp875 • encodings.cp932 • encodings.cp949 • encodings.cp950 • encodings.euc_jis_2004 • encodings.euc_jisx0213 • encodings.euc_jp • encodings.euc_kr • encodings.gb18030 • encodings.gb2312 • encodings.gbk • encodings.hex_codec • encodings.hp_roman8 • encodings.hz • encodings.idna • encodings.iso2022_jp • encodings.iso2022_jp_1 • encodings.iso2022_jp_2 • encodings.iso2022_jp_2004 • encodings.iso2022_jp_3 • encodings.iso2022_jp_ext • encodings.iso2022_kr • encodings.iso8859_1 • encodings.iso8859_10 • encodings.iso8859_11 • encodings.iso8859_13 • encodings.iso8859_14 • encodings.iso8859_15 • encodings.iso8859_16 • encodings.iso8859_2 • encodings.iso8859_3 • encodings.iso8859_4 • encodings.iso8859_5 • encodings.iso8859_6 • encodings.iso8859_7 • encodings.iso8859_8 • encodings.iso8859_9 • encodings.johab • encodings.koi8_r • encodings.koi8_t • encodings.koi8_u • encodings.kz1048 • encodings.latin_1 • encodings.mac_arabic • encodings.mac_croatian • encodings.mac_cyrillic • encodings.mac_farsi • encodings.mac_greek • encodings.mac_iceland • encodings.mac_latin2 • encodings.mac_roman • encodings.mac_romanian • encodings.mac_turkish • encodings.mbcs • encodings.oem • encodings.palmos • encodings.ptcp154 • encodings.punycode • encodings.quopri_codec • encodings.raw_unicode_escape • encodings.rot_13 • encodings.shift_jis • encodings.shift_jis_2004 • encodings.shift_jisx0213 • encodings.tis_620 • encodings.undefined • encodings.unicode_escape • encodings.utf_16 • encodings.utf_16_be • encodings.utf_16_le • encodings.utf_32 • encodings.utf_32_be • encodings.utf_32_le • encodings.utf_7 • encodings.utf_8 • encodings.utf_8_sig • encodings.uu_codec • encodings.zlib_codec • init.py • locale

encodings.aliases SourceModule

imports: encodings

imported by: encodings • init.py • locale

encodings.ascii SourceModule

imports: codecs • encodings

imported by: encodings • init.py

encodings.base64_codec SourceModule

imports: base64 • codecs • encodings

imported by: encodings • init.py

encodings.big5 SourceModule

imports: _codecs_tw • _multibytecodec • codecs • encodings

imported by: encodings • init.py

encodings.big5hkscs SourceModule

imports: _codecs_hk • _multibytecodec • codecs • encodings

imported by: encodings • init.py

encodings.bz2_codec SourceModule

imports: bz2 • codecs • encodings

imported by: encodings • init.py

encodings.charmap SourceModule

imports: codecs • encodings

imported by: encodings • init.py

encodings.cp037 SourceModule

imports: codecs • encodings

imported by: encodings • init.py

encodings.cp1006 SourceModule

imports: codecs • encodings

imported by: encodings • init.py

encodings.cp1026 SourceModule

imports: codecs • encodings

imported by: encodings • init.py

encodings.cp1125 SourceModule

imports: codecs • encodings

imported by: encodings • init.py

encodings.cp1140 SourceModule

imports: codecs • encodings

imported by: encodings • init.py

encodings.cp1250 SourceModule

imports: codecs • encodings

imported by: encodings • init.py

encodings.cp1251 SourceModule

imports: codecs • encodings

imported by: encodings • init.py

encodings.cp1252 SourceModule

imports: codecs • encodings

imported by: encodings • init.py

encodings.cp1253 SourceModule

imports: codecs • encodings

imported by: encodings • init.py

encodings.cp1254 SourceModule

imports: codecs • encodings

imported by: encodings • init.py

encodings.cp1255 SourceModule

imports: codecs • encodings

imported by: encodings • init.py

encodings.cp1256 SourceModule

imports: codecs • encodings

imported by: encodings • init.py

encodings.cp1257 SourceModule

imports: codecs • encodings

imported by: encodings • init.py

encodings.cp1258 SourceModule

imports: codecs • encodings

imported by: encodings • init.py

encodings.cp273 SourceModule

imports: codecs • encodings

imported by: encodings • init.py

encodings.cp424 SourceModule

imports: codecs • encodings

imported by: encodings • init.py

encodings.cp437 SourceModule

imports: codecs • encodings

imported by: encodings • init.py

encodings.cp500 SourceModule

imports: codecs • encodings

imported by: encodings • init.py

encodings.cp720 SourceModule

imports: codecs • encodings

imported by: encodings • init.py

encodings.cp737 SourceModule

imports: codecs • encodings

imported by: encodings • init.py

encodings.cp775 SourceModule

imports: codecs • encodings

imported by: encodings • init.py

encodings.cp850 SourceModule

imports: codecs • encodings

imported by: encodings • init.py

encodings.cp852 SourceModule

imports: codecs • encodings

imported by: encodings • init.py

encodings.cp855 SourceModule

imports: codecs • encodings

imported by: encodings • init.py

encodings.cp856 SourceModule

imports: codecs • encodings

imported by: encodings • init.py

encodings.cp857 SourceModule

imports: codecs • encodings

imported by: encodings • init.py

encodings.cp858 SourceModule

imports: codecs • encodings

imported by: encodings • init.py

encodings.cp860 SourceModule

imports: codecs • encodings

imported by: encodings • init.py

encodings.cp861 SourceModule

imports: codecs • encodings

imported by: encodings • init.py

encodings.cp862 SourceModule

imports: codecs • encodings

imported by: encodings • init.py

encodings.cp863 SourceModule

imports: codecs • encodings

imported by: encodings • init.py

encodings.cp864 SourceModule

imports: codecs • encodings

imported by: encodings • init.py

encodings.cp865 SourceModule

imports: codecs • encodings

imported by: encodings • init.py

encodings.cp866 SourceModule

imports: codecs • encodings

imported by: encodings • init.py

encodings.cp869 SourceModule

imports: codecs • encodings

imported by: encodings • init.py

encodings.cp874 SourceModule

imports: codecs • encodings

imported by: encodings • init.py

encodings.cp875 SourceModule

imports: codecs • encodings

imported by: encodings • init.py

encodings.cp932 SourceModule

imports: _codecs_jp • _multibytecodec • codecs • encodings

imported by: encodings • init.py

encodings.cp949 SourceModule

imports: _codecs_kr • _multibytecodec • codecs • encodings

imported by: encodings • init.py

encodings.cp950 SourceModule

imports: _codecs_tw • _multibytecodec • codecs • encodings

imported by: encodings • init.py

encodings.euc_jis_2004 SourceModule

imports: _codecs_jp • _multibytecodec • codecs • encodings

imported by: encodings • init.py

encodings.euc_jisx0213 SourceModule

imports: _codecs_jp • _multibytecodec • codecs • encodings

imported by: encodings • init.py

encodings.euc_jp SourceModule

imports: _codecs_jp • _multibytecodec • codecs • encodings

imported by: encodings • init.py

encodings.euc_kr SourceModule

imports: _codecs_kr • _multibytecodec • codecs • encodings

imported by: encodings • init.py

encodings.gb18030 SourceModule

imports: _codecs_cn • _multibytecodec • codecs • encodings

imported by: encodings • init.py

encodings.gb2312 SourceModule

imports: _codecs_cn • _multibytecodec • codecs • encodings

imported by: encodings • init.py

encodings.gbk SourceModule

imports: _codecs_cn • _multibytecodec • codecs • encodings

imported by: encodings • init.py

encodings.hex_codec SourceModule

imports: binascii • codecs • encodings

imported by: encodings • init.py

encodings.hp_roman8 SourceModule

imports: codecs • encodings

imported by: encodings • init.py

encodings.hz SourceModule

imports: _codecs_cn • _multibytecodec • codecs • encodings

imported by: encodings • init.py

encodings.idna SourceModule

imports: codecs • encodings • re • stringprep • unicodedata

imported by: encodings • init.py

encodings.iso2022_jp SourceModule

imports: _codecs_iso2022 • _multibytecodec • codecs • encodings

imported by: encodings • init.py

encodings.iso2022_jp_1 SourceModule

imports: _codecs_iso2022 • _multibytecodec • codecs • encodings

imported by: encodings • init.py

encodings.iso2022_jp_2 SourceModule

imports: _codecs_iso2022 • _multibytecodec • codecs • encodings

imported by: encodings • init.py

encodings.iso2022_jp_2004 SourceModule

imports: _codecs_iso2022 • _multibytecodec • codecs • encodings

imported by: encodings • init.py

encodings.iso2022_jp_3 SourceModule

imports: _codecs_iso2022 • _multibytecodec • codecs • encodings

imported by: encodings • init.py

encodings.iso2022_jp_ext SourceModule

imports: _codecs_iso2022 • _multibytecodec • codecs • encodings

imported by: encodings • init.py

encodings.iso2022_kr SourceModule

imports: _codecs_iso2022 • _multibytecodec • codecs • encodings

imported by: encodings • init.py

encodings.iso8859_1 SourceModule

imports: codecs • encodings

imported by: encodings • init.py

encodings.iso8859_10 SourceModule

imports: codecs • encodings

imported by: encodings • init.py

encodings.iso8859_11 SourceModule

imports: codecs • encodings

imported by: encodings • init.py

encodings.iso8859_13 SourceModule

imports: codecs • encodings

imported by: encodings • init.py

encodings.iso8859_14 SourceModule

imports: codecs • encodings

imported by: encodings • init.py

encodings.iso8859_15 SourceModule

imports: codecs • encodings

imported by: encodings • init.py

encodings.iso8859_16 SourceModule

imports: codecs • encodings

imported by: encodings • init.py

encodings.iso8859_2 SourceModule

imports: codecs • encodings

imported by: encodings • init.py

encodings.iso8859_3 SourceModule

imports: codecs • encodings

imported by: encodings • init.py

encodings.iso8859_4 SourceModule

imports: codecs • encodings

imported by: encodings • init.py

encodings.iso8859_5 SourceModule

imports: codecs • encodings

imported by: encodings • init.py

encodings.iso8859_6 SourceModule

imports: codecs • encodings

imported by: encodings • init.py

encodings.iso8859_7 SourceModule

imports: codecs • encodings

imported by: encodings • init.py

encodings.iso8859_8 SourceModule

imports: codecs • encodings

imported by: encodings • init.py

encodings.iso8859_9 SourceModule

imports: codecs • encodings

imported by: encodings • init.py

encodings.johab SourceModule

imports: _codecs_kr • _multibytecodec • codecs • encodings

imported by: encodings • init.py

encodings.koi8_r SourceModule

imports: codecs • encodings

imported by: encodings • init.py

encodings.koi8_t SourceModule

imports: codecs • encodings

imported by: encodings • init.py

encodings.koi8_u SourceModule

imports: codecs • encodings

imported by: encodings • init.py

encodings.kz1048 SourceModule

imports: codecs • encodings

imported by: encodings • init.py

encodings.latin_1 SourceModule

imports: codecs • encodings

imported by: encodings • init.py

encodings.mac_arabic SourceModule

imports: codecs • encodings

imported by: encodings • init.py

encodings.mac_croatian SourceModule

imports: codecs • encodings

imported by: encodings • init.py

encodings.mac_cyrillic SourceModule

imports: codecs • encodings

imported by: encodings • init.py

encodings.mac_farsi SourceModule

imports: codecs • encodings

imported by: encodings • init.py

encodings.mac_greek SourceModule

imports: codecs • encodings

imported by: encodings • init.py

encodings.mac_iceland SourceModule

imports: codecs • encodings

imported by: encodings • init.py

encodings.mac_latin2 SourceModule

imports: codecs • encodings

imported by: encodings • init.py

encodings.mac_roman SourceModule

imports: codecs • encodings

imported by: encodings • init.py

encodings.mac_romanian SourceModule

imports: codecs • encodings

imported by: encodings • init.py

encodings.mac_turkish SourceModule

imports: codecs • encodings

imported by: encodings • init.py

encodings.mbcs SourceModule

imports: codecs • encodings

imported by: encodings • init.py

encodings.oem SourceModule

imports: codecs • encodings

imported by: encodings • init.py

encodings.palmos SourceModule

imports: codecs • encodings

imported by: encodings • init.py

encodings.ptcp154 SourceModule

imports: codecs • encodings

imported by: encodings • init.py

encodings.punycode SourceModule

imports: codecs • encodings

imported by: encodings • init.py

encodings.quopri_codec SourceModule

imports: codecs • encodings • io • quopri

imported by: encodings • init.py

encodings.raw_unicode_escape SourceModule

imports: codecs • encodings

imported by: encodings • init.py

encodings.rot_13 SourceModule

imports: codecs • encodings • sys

imported by: encodings • init.py

encodings.shift_jis SourceModule

imports: _codecs_jp • _multibytecodec • codecs • encodings

imported by: encodings • init.py

encodings.shift_jis_2004 SourceModule

imports: _codecs_jp • _multibytecodec • codecs • encodings

imported by: encodings • init.py

encodings.shift_jisx0213 SourceModule

imports: _codecs_jp • _multibytecodec • codecs • encodings

imported by: encodings • init.py

encodings.tis_620 SourceModule

imports: codecs • encodings

imported by: encodings • init.py

encodings.undefined SourceModule

imports: codecs • encodings

imported by: encodings • init.py

encodings.unicode_escape SourceModule

imports: codecs • encodings

imported by: encodings • init.py

encodings.utf_16 SourceModule

imports: codecs • encodings • sys

imported by: encodings • init.py

encodings.utf_16_be SourceModule

imports: codecs • encodings

imported by: encodings • init.py

encodings.utf_16_le SourceModule

imports: codecs • encodings

imported by: encodings • init.py

encodings.utf_32 SourceModule

imports: codecs • encodings • sys

imported by: encodings • init.py

encodings.utf_32_be SourceModule

imports: codecs • encodings

imported by: encodings • init.py

encodings.utf_32_le SourceModule

imports: codecs • encodings

imported by: encodings • init.py

encodings.utf_7 SourceModule

imports: codecs • encodings

imported by: encodings • init.py

encodings.utf_8 SourceModule

imports: codecs • encodings

imported by: encodings • init.py

encodings.utf_8_sig SourceModule

imports: codecs • encodings

imported by: encodings • init.py

encodings.uu_codec SourceModule

imports: binascii • codecs • encodings • io

imported by: encodings • init.py

encodings.zlib_codec SourceModule

imports: codecs • encodings • zlib

imported by: encodings • init.py

enum SourceModule

imports: sys • types • warnings

imported by: ast • http • init.py • inspect • py_compile • re • signal • socket • ssl

errno (builtin module)

imported by: gettext • gzip • pathlib • serial.serialposix • shutil • socket • ssl • subprocess • tempfile

fcntl MissingModule

imported by: serial.serialposix • subprocess

fnmatch SourceModule

imports: functools • itertools • os • posixpath • re

imported by: glob • pathlib • shutil • tracemalloc • urllib.request

fractions SourceModule

imports: decimal • math • numbers • operator • re • sys

imported by: statistics

ftplib SourceModule

imports: netrc • re • socket • ssl • sys • warnings

imported by: urllib.request

functools SourceModule

imports: _functools • _thread • abc • collections • reprlib • types • typing • weakref

imported by: contextlib • copyreg • dataclasses • email._encoded_words • email.charset • fnmatch • importlib.metadata • importlib.metadata._functools • importlib.util • init.py • inspect • linecache • locale • operator • pathlib • pickle • pkgutil • re • signal • tempfile • threading • tokenize • tracemalloc • types • typing

gc (builtin module)

imports: time

imported by: _posixsubprocess • weakref

genericpath SourceModule

imports: os • stat

imported by: init.py • ntpath • posixpath

getopt SourceModule

imports: gettext • os • sys

imported by: base64 • mimetypes • quopri

getpass SourceModule

imports: contextlib • io • msvcrt • os • pwd • sys • termios • warnings

imported by: urllib.request

gettext SourceModule

imports: builtins • copy • errno • locale • os • re • struct • sys • warnings

imported by: argparse • getopt • optparse

glob SourceModule

imports: contextlib • fnmatch • itertools • os • re • stat • sys

imported by: serial.tools.list_ports_linux • serial.tools.list_ports_posix

grp MissingModule

imported by: pathlib • shutil • subprocess • tarfile

gzip SourceModule

imports: _compression • argparse • builtins • errno • io • os • struct • sys • time • warnings • zlib

imported by: tarfile

hashlib SourceModule

imports: _blake2 • _hashlib • _md5 • _sha1 • _sha256 • _sha3 • _sha512 • logging • warnings

imported by: random • urllib.request

heapq SourceModule

imports: _heapq

imported by: collections • init.py

http Package

imports: enum

imported by: http.client • http.cookiejar

http.client SourceModule

imports: collections.abc • email.message • email.parser • http • io • re • socket • ssl • sys • urllib.parse • warnings

imported by: http.cookiejar • urllib.request

http.cookiejar SourceModule

imports: calendar • copy • datetime • http • http.client • io • logging • os • re • threading • time • traceback • urllib.parse • urllib.request • warnings

imported by: urllib.request

importlib Package

imports: _frozen_importlib • _frozen_importlib_external • _imp • importlib • importlib._bootstrap • importlib._bootstrap_external • importlib.abc • importlib.machinery • sys • warnings

imported by: importlib • importlib._abc • importlib._bootstrap • importlib._bootstrap_external • importlib.abc • importlib.machinery • importlib.metadata • importlib.readers • importlib.util • inspect • pkgutil • serial

importlib._abc SourceModule

imports: abc • importlib • importlib._bootstrap • warnings

imported by: importlib.abc • importlib.util

importlib._bootstrap SourceModule

imports: _frozen_importlib_external • importlib

imported by: importlib • importlib._abc • importlib.machinery • importlib.util

importlib._bootstrap_external SourceModule

imports: _imp • _io • _warnings • importlib • importlib.metadata • importlib.readers • marshal • nt • posix • sys • tokenize • winreg

imported by: importlib • importlib.abc • importlib.machinery • importlib.util • py_compile

importlib.abc SourceModule

imports: _frozen_importlib • _frozen_importlib_external • abc • importlib • importlib._abc • importlib._bootstrap_external • importlib.machinery • typing • warnings

imported by: importlib • importlib.metadata • importlib.readers

importlib.machinery SourceModule

imports: importlib • importlib._bootstrap • importlib._bootstrap_external

imported by: ctypes.util • importlib • importlib.abc • inspect • pkgutil • py_compile

importlib.metadata Package

imports: abc • collections • contextlib • csv • email • functools • importlib • importlib.abc • importlib.metadata • importlib.metadata._adapters • importlib.metadata._collections • importlib.metadata._functools • importlib.metadata._itertools • importlib.metadata._meta • itertools • operator • os • pathlib • pep517 • posixpath • re • sys • textwrap • typing • warnings • zipfile

imported by: importlib._bootstrap_external • importlib.metadata • importlib.metadata._adapters • importlib.metadata._collections • importlib.metadata._functools • importlib.metadata._itertools • importlib.metadata._meta • importlib.metadata._text

importlib.metadata._adapters SourceModule

imports: email.message • importlib.metadata • importlib.metadata._text • re • textwrap

imported by: importlib.metadata

importlib.metadata._collections SourceModule

imports: collections • importlib.metadata

imported by: importlib.metadata

importlib.metadata._functools SourceModule

imports: functools • importlib.metadata • types

imported by: importlib.metadata • importlib.metadata._text

importlib.metadata._itertools SourceModule

imports: importlib.metadata • itertools

imported by: importlib.metadata

importlib.metadata._meta SourceModule

imports: importlib.metadata • typing

imported by: importlib.metadata

importlib.metadata._text SourceModule

imports: importlib.metadata • importlib.metadata._functools • re

imported by: importlib.metadata._adapters

importlib.readers SourceModule

imports: collections • importlib • importlib.abc • pathlib • zipfile

imported by: importlib._bootstrap_external • zipimport

importlib.util SourceModule

imports: _imp • contextlib • functools • importlib • importlib._abc • importlib._bootstrap • importlib._bootstrap_external • sys • types • warnings

imported by: pkgutil • py_compile • zipfile

inspect SourceModule

imports: abc • argparse • ast • builtins • collections • collections.abc • dis • enum • functools • importlib • importlib.machinery • itertools • linecache • operator • os • re • sys • token • tokenize • types • warnings

imported by: ast • dataclasses • pkgutil • pyi_rth_inspect.py

io SourceModule

imports: _io • abc • warnings

imported by: PyQt5.uic.port_v3.string_io • _compression • bz2 • csv • dis • email.feedparser • email.generator • email.iterators • email.message • email.parser • encodings.quopri_codec • encodings.uu_codec • getpass • gzip • http.client • http.cookiejar • init.py • logging • lzma • os • pathlib • pickle • pprint • quopri • serial.serialutil • shlex • socket • subprocess • tarfile • tempfile • tokenize • urllib.request • xml.etree.ElementTree • xml.sax • xml.sax.saxutils • zipfile

itertools (builtin module)

imported by: _pydecimal • calendar • collections • ctypes.macholib.dyld • fnmatch • glob • importlib.metadata • importlib.metadata._itertools • inspect • pickle • random • reprlib • statistics • threading • tokenize • traceback • weakref • zipfile

java MissingModule

imported by: xml.sax._exceptions

keyword SourceModule

imported by: collections • dataclasses • init.py

linecache SourceModule

imports: functools • os • sys • tokenize

imported by: init.py • inspect • traceback • tracemalloc • warnings

locale SourceModule

imports: _collections_abc • _locale • builtins • encodings • encodings.aliases • functools • os • re • sys • warnings

imported by: _pydecimal • _strptime • calendar • gettext • init.py • xml.etree.ElementTree

logging Package

imports: atexit • collections.abc • io • os • pickle • re • string • sys • threading • time • traceback • warnings • weakref

imported by: PyQt5.uic.Compiler.qobjectcreator • PyQt5.uic.properties • PyQt5.uic.uiparser • hashlib • http.cookiejar

lzma SourceModule

imports: _compression • _lzma • builtins • io • os

imported by: shutil • tarfile • zipfile

marshal (builtin module)

imported by: importlib._bootstrap_external • pkgutil • zipimport

math (builtin module)

imported by: _pydecimal • datetime • fractions • random • selectors • statistics

mimetypes SourceModule

imports: _winapi • getopt • os • posixpath • sys • urllib.parse • winreg

imported by: urllib.request

msvcrt (builtin module)

imported by: getpass • subprocess

netrc SourceModule

imports: os • pwd • shlex • stat

imported by: ftplib

nt (builtin module)

imported by: ctypes • importlib._bootstrap_external • ntpath • os • shutil

ntpath SourceModule

imports: genericpath • nt • os • stat • string • sys

imported by: init.py • ntpath • os • pathlib

ntpath AliasNode

imports: ntpath • os

imported by: PyQt5.uic.icon_cache • PyQt5.uic.objcreator • PyQt5.uic.properties • os • pkgutil • py_compile • tracemalloc

nturl2path SourceModule

imports: string • urllib.parse

imported by: urllib.request

numbers SourceModule

imports: abc

imported by: _pydecimal • fractions • statistics

opcode SourceModule

imports: _opcode

imported by: dis

operator SourceModule

imports: _operator • builtins • functools

imported by: collections • copyreg • datetime • email._header_value_parser • fractions • importlib.metadata • init.py • inspect • pathlib • random • statistics • typing

optparse SourceModule

imports: gettext • os • sys • textwrap

imported by: uu

org MissingModule

imported by: pickle

os SourceModule

imports: _collections_abc • abc • io • nt • ntpath • ntpath • posix • posixpath • stat • subprocess • sys • warnings

imported by: PyQt5 • PyQt5.uic • PyQt5.uic.uiparser • argparse • bz2 • ctypes • ctypes._aix • ctypes.macholib.dyld • ctypes.util • email.utils • fnmatch • genericpath • getopt • getpass • gettext • glob • gzip • http.cookiejar • importlib.metadata • init.py • inspect • linecache • locale • logging • lzma • mimetypes • netrc • ntpath • ntpath • optparse • pathlib • pkgutil • posixpath • py_compile • pyi_rth_inspect.py • pyi_rth_pkgutil.py • pyi_rth_pyqt5.py • random • serial • serial.serialposix • serial.tools.list_ports • serial.tools.list_ports_linux • serial.tools.list_ports_posix • shlex • shutil • socket • ssl • subprocess • tarfile • tempfile • threading • urllib.request • uu • xml.sax • xml.sax.saxutils • zipfile • zipimport

pathlib SourceModule

imports: _collections_abc • errno • fnmatch • functools • grp • io • ntpath • operator • os • posixpath • pwd • re • stat • sys • urllib.parse • warnings

imported by: importlib.metadata • importlib.readers • zipfile

pep517 MissingModule

imported by: importlib.metadata

pickle SourceModule

imports: _compat_pickle • _pickle • codecs • copyreg • functools • io • itertools • org • pprint • re • struct • sys • types

imported by: logging • tracemalloc

pkgutil SourceModule

imports: collections • functools • importlib • importlib.machinery • importlib.util • inspect • marshal • ntpath • os • re • sys • types • warnings • zipimport

imported by: PyQt5 • pyi_rth_pkgutil.py

port_v2 MissingModule

imported by: PyQt5.uic.properties

posix MissingModule

imports: resource

imported by: importlib._bootstrap_external • os • shutil

posixpath SourceModule

imports: genericpath • os • pwd • re • stat • sys

imported by: fnmatch • importlib.metadata • init.py • mimetypes • os • pathlib • urllib.request • zipfile

pprint SourceModule

imports: collections • dataclasses • io • re • sys • time • types

imported by: pickle

pwd MissingModule

imported by: getpass • netrc • pathlib • posixpath • shutil • subprocess • tarfile

py_compile SourceModule

imports: argparse • enum • importlib._bootstrap_external • importlib.machinery • importlib.util • ntpath • os • sys • traceback

imported by: zipfile

pyexpat C:\Users\daron\AppData\Local\Programs\Python\Python310\DLLs\pyexpat.pyd

imported by: _elementtree • xml.etree.ElementTree • xml.parsers.expat

pyimod02_importers MissingModule

imported by: pyi_rth_pkgutil.py

quopri SourceModule

imports: binascii • getopt • io • sys

imported by: email.encoders • email.message • encodings.quopri_codec

random SourceModule

imports: _collections_abc • _random • _sha512 • bisect • hashlib • itertools • math • operator • os • statistics • time • warnings

imported by: email.generator • email.utils • statistics • tempfile

re SourceModule

imports: _locale • copyreg • enum • functools • sre_compile • sre_constants • sre_parse

imported by: PyQt5.uic.Compiler.qtproxies • PyQt5.uic.port_v2.as_string • PyQt5.uic.port_v3.as_string • PyQt5.uic.uiparser • _pydecimal • _sre • _strptime • argparse • base64 • csv • ctypes._aix • ctypes.macholib.dylib • ctypes.macholib.framework • ctypes.util • dataclasses • email._encoded_words • email._header_value_parser • email.feedparser • email.generator • email.header • email.message • email.policy • email.quoprimime • email.utils • encodings.idna • fnmatch • fractions • ftplib • gettext • glob • http.client • http.cookiejar • importlib.metadata • importlib.metadata._adapters • importlib.metadata._text • init.py • inspect • locale • logging • pathlib • pickle • pkgutil • posixpath • pprint • serial.tools.list_ports • serial.tools.list_ports_common • serial.tools.list_ports_windows • shlex • string • tarfile • textwrap • tokenize • typing • urllib.parse • urllib.request • warnings • xml.etree.ElementPath • xml.etree.ElementTree

reprlib SourceModule

imports: _thread • builtins • itertools

imported by: collections • functools • init.py

resource MissingModule

imported by: posix

select C:\Users\daron\AppData\Local\Programs\Python\Python310\DLLs\select.pyd

imported by: selectors • serial.serialposix • subprocess

selectors SourceModule

imports: abc • collections • collections.abc • math • select • sys

imported by: socket • subprocess

serial Package

imports: importlib • os • serial.serialcli • serial.serialjava • serial.serialposix • serial.serialutil • serial.serialwin32 • serial.win32 • sys

imported by: init.py • serial.serialcli • serial.serialjava • serial.serialposix • serial.serialutil • serial.serialwin32 • serial.tools • serial.tools.list_ports_posix • serial.tools.list_ports_windows • serial.win32

serial.serialcli SourceModule

imports: 'System.IO' • System • serial • serial.serialutil

imported by: serial

serial.serialjava SourceModule

imports: serial • serial.serialutil

imported by: serial

serial.serialposix SourceModule

imports: array • errno • fcntl • os • select • serial • serial.serialutil • struct • sys • termios • warnings

imported by: serial

serial.serialutil SourceModule

imports: array • io • serial • sys • time

imported by: serial • serial.serialcli • serial.serialjava • serial.serialposix • serial.serialwin32

serial.serialwin32 SourceModule

imports: ctypes • serial • serial.serialutil • serial.win32 • time

imported by: serial

serial.tools Package

imports: serial • serial.tools.list_ports_common

imported by: serial.tools.list_ports • serial.tools.list_ports_common • serial.tools.list_ports_linux • serial.tools.list_ports_osx • serial.tools.list_ports_posix • serial.tools.list_ports_windows

serial.tools.list_ports SourceModule

imports: argparse • os • re • serial.tools • serial.tools.list_ports_posix • serial.tools.list_ports_windows • sys

imported by: init.py

serial.tools.list_ports_common SourceModule

imports: re • serial.tools

imported by: serial.tools • serial.tools.list_ports_linux • serial.tools.list_ports_osx • serial.tools.list_ports_posix • serial.tools.list_ports_windows

serial.tools.list_ports_linux SourceModule

imports: glob • os • serial.tools • serial.tools.list_ports_common

imported by: serial.tools.list_ports_posix

serial.tools.list_ports_osx SourceModule

imports: ctypes • ctypes.util • serial.tools • serial.tools.list_ports_common

imported by: serial.tools.list_ports_posix

serial.tools.list_ports_posix SourceModule

imports: glob • os • serial • serial.tools • serial.tools.list_ports_common • serial.tools.list_ports_linux • serial.tools.list_ports_osx • sys

imported by: serial.tools.list_ports

serial.tools.list_ports_windows SourceModule

imports: ctypes • ctypes.wintypes • re • serial • serial.tools • serial.tools.list_ports_common • serial.win32

imported by: serial.tools.list_ports

serial.win32 SourceModule

imports: ctypes • ctypes.wintypes • serial

imported by: serial • serial.serialwin32 • serial.tools.list_ports_windows

shlex SourceModule

imports: collections • io • os • re • sys • warnings

imported by: netrc

shutil SourceModule

imports: bz2 • collections • errno • fnmatch • grp • lzma • nt • os • posix • pwd • stat • sys • tarfile • zipfile • zlib

imported by: argparse • ctypes.util • tarfile • tempfile • zipfile

signal SourceModule

imports: _signal • enum • functools

imported by: subprocess

socket SourceModule

imports: _socket • array • enum • errno • io • os • selectors • sys

imported by: _ssl • email.utils • ftplib • http.client • ssl • urllib.request

sre_compile SourceModule

imports: _sre • sre_constants • sre_parse • sys

imported by: init.py • re

sre_constants SourceModule

imports: _sre

imported by: init.py • re • sre_compile • sre_parse

sre_parse SourceModule

imports: sre_constants • unicodedata • warnings

imported by: init.py • re • sre_compile

ssl SourceModule

imports: _ssl • base64 • calendar • collections • enum • errno • os • socket • sys • time • warnings

imported by: ftplib • http.client • urllib.request

stat SourceModule

imports: _stat

imported by: genericpath • glob • init.py • netrc • ntpath • os • pathlib • posixpath • shutil • tarfile • zipfile

statistics SourceModule

imports: _statistics • bisect • collections • decimal • fractions • itertools • math • numbers • operator • random

imported by: random

string SourceModule

imports: _string • collections • re

imported by: email._encoded_words • email._header_value_parser • email.quoprimime • logging • ntpath • nturl2path • urllib.request

stringprep SourceModule

imports: unicodedata

imported by: encodings.idna

struct SourceModule

imports: _struct

imported by: base64 • ctypes • ctypes.util • gettext • gzip • pickle • serial.serialposix • tarfile • zipfile

subprocess SourceModule

imports: _posixsubprocess • _winapi • builtins • contextlib • errno • fcntl • grp • io • msvcrt • os • pwd • select • selectors • signal • sys • threading • time • types • warnings

imported by: ctypes._aix • ctypes.util • os

sys (builtin module)

imported by: PyQt5 • PyQt5.uic • PyQt5.uic.Compiler.compiler • PyQt5.uic.Compiler.qobjectcreator • PyQt5.uic.Compiler.qtproxies • PyQt5.uic.Loader.qobjectcreator • PyQt5.uic.properties • PyQt5.uic.uiparser • _collections_abc • _compression • _pydecimal • argparse • ast • base64 • calendar • codecs • collections • contextlib • ctypes • ctypes._aix • ctypes._endian • ctypes.util • dataclasses • datetime • dis • email._header_value_parser • email.generator • email.iterators • email.policy • encodings • encodings.rot_13 • encodings.utf_16 • encodings.utf_32 • enum • fractions • ftplib • getopt • getpass • gettext • glob • gzip • http.client • importlib • importlib._bootstrap_external • importlib.metadata • importlib.util • init.py • inspect • linecache • locale • logging • mimetypes • ntpath • optparse • os • pathlib • pickle • pkgutil • posixpath • pprint • py_compile • pyi_rth_inspect.py • pyi_rth_pkgutil.py • pyi_rth_pyqt5.py • quopri • selectors • serial • serial.serialposix • serial.serialutil • serial.tools.list_ports • serial.tools.list_ports_posix • shlex • shutil • socket • sre_compile • ssl • subprocess • tarfile • tempfile • threading • tokenize • traceback • types • typing • urllib.parse • urllib.request • uu • warnings • weakref • xml.etree.ElementTree • xml.parsers.expat • xml.sax • xml.sax._exceptions • xml.sax.expatreader • xml.sax.saxutils • zipfile • zipimport

tarfile SourceModule

imports: argparse • builtins • bz2 • copy • grp • gzip • io • lzma • os • pwd • re • shutil • stat • struct • sys • time • zlib

imported by: shutil

tempfile SourceModule

imports: _thread • errno • functools • io • os • random • shutil • sys • types • warnings • weakref

imported by: ctypes.util • urllib.request • urllib.response

termios MissingModule

imported by: getpass • serial.serialposix

textwrap SourceModule

imports: re

imported by: argparse • importlib.metadata • importlib.metadata._adapters • optparse

threading SourceModule

imports: _collections • _thread • _threading_local • _weakrefset • collections • functools • itertools • os • sys • time • traceback • warnings

imported by: _threading_local • http.cookiejar • logging • subprocess • zipfile

time (builtin module)

imports: _strptime

imported by: _datetime • _strptime • datetime • email._parseaddr • email.generator • email.utils • gc • gzip • http.cookiejar • init.py • logging • pprint • random • serial.serialutil • serial.serialwin32 • ssl • subprocess • tarfile • threading • urllib.request • zipfile • zipimport

token SourceModule

imported by: inspect • tokenize

tokenize SourceModule

imports: argparse • builtins • codecs • collections • functools • io • itertools • re • sys • token

imported by: importlib._bootstrap_external • inspect • linecache

traceback SourceModule

imports: collections • itertools • linecache • sys

imported by: http.cookiejar • init.py • logging • py_compile • threading • warnings

tracemalloc SourceModule

imports: _tracemalloc • collections.abc • fnmatch • functools • linecache • ntpath • pickle

imported by: warnings

types SourceModule

imports: _collections_abc • functools • sys

imported by: _weakrefset • contextlib • copy • ctypes • dataclasses • dis • email.headerregistry • enum • functools • importlib.metadata._functools • importlib.util • init.py • inspect • pickle • pkgutil • pprint • subprocess • tempfile • typing • urllib.parse

typing SourceModule

imports: abc • collections • collections.abc • contextlib • functools • operator • re • sys • types

imported by: functools • importlib.abc • importlib.metadata • importlib.metadata._meta

unicodedata C:\Users\daron\AppData\Local\Programs\Python\Python310\DLLs\unicodedata.pyd

imported by: encodings.idna • sre_parse • stringprep • urllib.parse

urllib Package

imported by: email._header_value_parser • urllib.error • urllib.parse • urllib.request • urllib.response

urllib.error SourceModule

imports: urllib • urllib.response

imported by: urllib.request

urllib.parse SourceModule

imports: collections • re • sys • types • unicodedata • urllib • warnings

imported by: email.utils • http.client • http.cookiejar • mimetypes • nturl2path • pathlib • urllib.request • xml.etree.ElementInclude • xml.sax.saxutils

urllib.request SourceModule

imports: _scproxy • base64 • bisect • contextlib • email • email.utils • fnmatch • ftplib • getpass • hashlib • http.client • http.cookiejar • io • mimetypes • nturl2path • os • posixpath • re • socket • ssl • string • sys • tempfile • time • urllib • urllib.error • urllib.parse • urllib.response • warnings • winreg

imported by: http.cookiejar • xml.sax.saxutils

urllib.response SourceModule

imports: tempfile • urllib

imported by: urllib.error • urllib.request

uu SourceModule

imports: binascii • optparse • os • sys

imported by: email.message

warnings SourceModule

imports: _warnings • builtins • linecache • re • sys • traceback • tracemalloc

imported by: argparse • ast • enum • ftplib • getpass • gettext • gzip • hashlib • http.client • http.cookiejar • importlib • importlib._abc • importlib.abc • importlib.metadata • importlib.util • init.py • inspect • io • locale • logging • os • pathlib • pkgutil • random • serial.serialposix • shlex • sre_parse • ssl • subprocess • tempfile • threading • urllib.parse • urllib.request • xml.etree.ElementTree • zipfile

weakref SourceModule

imports: _collections_abc • _weakref • _weakrefset • atexit • copy • gc • itertools • sys

imported by: _threading_local • copy • functools • init.py • logging • tempfile • xml.sax.expatreader

winreg (builtin module)

imported by: importlib._bootstrap_external • mimetypes • urllib.request

xml Package

imports: xml.sax.expatreader • xml.sax.xmlreader

imported by: xml.etree • xml.parsers • xml.sax

xml.etree Package

imports: xml • xml.etree • xml.etree.ElementPath • xml.etree.ElementTree

imported by: xml.etree • xml.etree.ElementInclude • xml.etree.ElementPath • xml.etree.ElementTree • xml.etree.cElementTree

xml.etree.ElementInclude SourceModule

imports: copy • urllib.parse • xml.etree • xml.etree.ElementTree

imported by: _elementtree

xml.etree.ElementPath SourceModule

imports: re • xml.etree

imported by: _elementtree • xml.etree • xml.etree.ElementTree

xml.etree.ElementTree SourceModule

imports: _elementtree • collections • collections.abc • contextlib • io • locale • pyexpat • re • sys • warnings • xml.etree • xml.etree.ElementPath • xml.parsers • xml.parsers.expat

imported by: PyQt5.uic.uiparser • _elementtree • xml.etree • xml.etree.ElementInclude • xml.etree.cElementTree

xml.etree.cElementTree SourceModule

imports: xml.etree • xml.etree.ElementTree

imported by: _elementtree

xml.parsers Package

imports: xml • xml.parsers.expat

imported by: xml.etree.ElementTree • xml.parsers.expat • xml.sax.expatreader

xml.parsers.expat SourceModule

imports: pyexpat • sys • xml.parsers

imported by: xml.etree.ElementTree • xml.parsers • xml.sax.expatreader

xml.sax Package

imports: 'org.python' • io • os • sys • xml • xml.sax • xml.sax._exceptions • xml.sax.expatreader • xml.sax.handler • xml.sax.saxutils • xml.sax.xmlreader

imported by: xml.sax • xml.sax._exceptions • xml.sax.expatreader • xml.sax.handler • xml.sax.saxutils • xml.sax.xmlreader

xml.sax._exceptions SourceModule

imports: java • sys • xml.sax

imported by: xml.sax • xml.sax.expatreader • xml.sax.xmlreader

xml.sax.expatreader SourceModule

imports: _weakref • sys • weakref • xml.parsers • xml.parsers.expat • xml.sax • xml.sax._exceptions • xml.sax.handler • xml.sax.saxutils • xml.sax.xmlreader

imported by: xml • xml.sax

xml.sax.handler SourceModule

imports: xml.sax

imported by: xml.sax • xml.sax.expatreader • xml.sax.saxutils • xml.sax.xmlreader

xml.sax.saxutils SourceModule

imports: codecs • io • os • sys • urllib.parse • urllib.request • xml.sax • xml.sax.handler • xml.sax.xmlreader

imported by: xml.sax • xml.sax.expatreader • xml.sax.xmlreader

xml.sax.xmlreader SourceModule

imports: xml.sax • xml.sax._exceptions • xml.sax.handler • xml.sax.saxutils

imported by: xml • xml.sax • xml.sax.expatreader • xml.sax.saxutils

zipfile SourceModule

imports: argparse • binascii • bz2 • contextlib • importlib.util • io • itertools • lzma • os • pathlib • posixpath • py_compile • shutil • stat • struct • sys • threading • time • warnings • zlib

imported by: importlib.metadata • importlib.readers • shutil

zipimport SourceModule

imports: _frozen_importlib • _frozen_importlib_external • _imp • _io • _warnings • importlib.readers • marshal • os • sys • time • zlib

imported by: pkgutil

zlib (builtin module)

imported by: encodings.zlib_codec • gzip • shutil • tarfile • zipfile • zipimport

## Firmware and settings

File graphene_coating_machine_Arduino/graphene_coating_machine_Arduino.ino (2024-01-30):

#include <AccelStepper.h>

const int StepX = 2; // Pin configuration of steps for motor X
const int DirX = 5;  // Pin configuration of spinning direction for motor X

const int StepZ = 4; // Pin configuration of steps for motor Z
const int DirZ = 7; // Pin configuration of spinning direction for motor Z
const int EndStopZ = 9; // Pin cofiguration of limit switch for motor Z
int stateZ; // State of limit switch

int val = 0; // Value read by sensor
static String commandBuffer = ""; // Buffer for command sent from Python app
float KGforce = 0; // Force in kilograms
float Gforce = 0;  // Force in grams
int steps = 0; // Value of steps to spin a motor
int calibrationWeigth = 0; // Actual value determined based on the trend line function of the calibration curve
int zero = 0; // Value used to consider mass placed on spinning table
int sum = 0; // Value used for calculations of average measurments in precise downward movement
float reqWeight = 0; // Value of read mass in downward movement (considers value of variable "zero")

char receivedValue;
AccelStepper stepperX(1, StepX, DirX);
AccelStepper stepperZ(2, StepZ, DirZ);

void setup() {
  Serial.begin(9600);
  pinMode(EndStopZ, INPUT_PULLUP);
  pinMode(DirZ, OUTPUT);
  pinMode(StepZ, OUTPUT);

  stepperX.setMaxSpeed(10000); // Max speed of steps per second for motor Z
  stepperX.setAcceleration(500); // Acceleration of motor X

  stepperZ.setMaxSpeed(10000); // Max speed of steps per second for motor Z
  stepperZ.setAcceleration(500); // Acceleration of motor Z
}

void loop() {
    serialEvent();
}

void serialEvent() { // Reading command buffer until the end sign ":" 
    while (Serial.available() > 0) {
        char receivedChar = Serial.read();
        if (receivedChar == ':') { // Found sign of new line or ending previous commend 
            processCommand(commandBuffer); 
            commandBuffer = ""; // Clear buffer after processing
        } else {
            commandBuffer += receivedChar; // Add read sign to commend buffer
        }
    }
}

void processCommand(String command) {
  char firstChar = command.charAt(0);

  if (firstChar == 's') { // Reading once value of calculated mass
    val = analogRead(A5);
    calibrationWeigth = 0.00005 * pow(val, 3) - 0.0206 * pow(val, 2) + 4.3575 * val - 26.459; //Change if own calibration function is needed
    delay(100);
    Serial.println(calibrationWeigth);
  } 
  
  if (firstChar == 'p') { // Spinning the table with desired amount of steps 
    steps = command.substring(1).toInt();
    stepperX.moveTo(steps);
    stepperX.runToPosition();
    while (stepperX.run()) {}
    Serial.println("Koniec");
  } 

  if (firstChar == 'u') { // Moving upwards to limit switch
    digitalWrite(DirZ, HIGH); 
    stateZ = digitalRead(EndStopZ);

    if (stateZ == 1) {
      while (true) {
        for (int i = 0; i < 200; i++) { // Amount of steps on full revolut of motor Z axis
          digitalWrite(StepZ, HIGH);
          delayMicroseconds(1000);  // Delay between steps 
          digitalWrite(StepZ, LOW);
          delayMicroseconds(1000);  // Delay between steps
        }
        stateZ = digitalRead(EndStopZ);
        if (stateZ == 0) { //If limit switch is closed - stop the motor Z axis
          stepperZ.stop();
          break;
        }
      }
    }
    Serial.println("Koniec"); 
  }

  if (firstChar == 'd') { // Moving downwards (limited by pressure sensor)
    val = analogRead(A5);
    zero = 0.00005 * pow(val, 3) - 0.0206 * pow(val, 2) + 4.3575 * val - 26.459; // Change if own calibration function is needed
    digitalWrite(DirZ, LOW); 

    while (true) {
      for (int i = 0; i < 200; i++) { // Amount of steps on full revolut of motor Z axis
        digitalWrite(StepZ, HIGH);
        delayMicroseconds(1000);  // Delay between steps 
        digitalWrite(StepZ, LOW);
        delayMicroseconds(1000);  // Delay between steps
      }
      val = analogRead(A5);
      calibrationWeigth = 0.00005 * pow(val, 3) - 0.0206 * pow(val, 2) + 4.3575 * val - 26.459; // Change if own calibration function is needed
      reqWeight = calibrationWeigth  - zero;
      if (reqWeight > 400) { // If read actual value is high enough - stop the motor Z axis
        stepperZ.stop();
        break;
      }
    }
    Serial.println("Koniec"); 
  }

  if (firstChar == 'm') { // Precise downward movement to get the most accurate mass reading from sensor
    KGforce = command.substring(1).toFloat();
    Gforce = KGforce * 1000;

    if (Gforce >= 500) { // Realise the function only when the value of Gforce was specified
      digitalWrite(DirZ, HIGH); 
      stepperZ.move(500);
      stepperZ.runToPosition();

      val = analogRead(A5);
      calibrationWeigth = 0.00005 * pow(val, 3) - 0.0206 * pow(val, 2) + 4.3575 * val - 26.459; // Change if own calibration function is needed
      reqWeight = calibrationWeigth - zero; 
      delay(70);
      digitalWrite(DirZ, LOW); 
      while (reqWeight < 0.95*Gforce) { // Loop until getting specified Gforce value
        if (reqWeight > 0.7*Gforce) { // Move slower when weight value is getting closer to derired Gforce value
          stepperZ.move(-5);
        }
        else {
          stepperZ.move(-100);
        }
        stepperZ.runToPosition();
        sum = 0;
        reqWeight = 0;
        for (int i = 0; i < 10; i++) { // Make 10 mearurements, than calculate the average value of read weight
          val = analogRead(A5);
          delay(40);
          calibrationWeigth = 0.00005 * pow(val, 3) - 0.0206 * pow(val, 2) + 4.3575 * val - 26.459; // Change if own calibration function is needed
          reqWeight = calibrationWeigth - zero;
          sum = sum + reqWeight;
        }
        reqWeight = sum/10;
      }
    }
    Serial.println("Koniec");
  }

  if (firstChar == 'r') { // Move in Z axis with desired amount of steps
    digitalWrite(DirZ, HIGH); 
    steps = command.substring(1).toInt();
    stepperZ.moveTo(steps);
    stepperZ.runToPosition();
    while (stepperZ.run()) {}
    Serial.println("Koniec");
  }
}

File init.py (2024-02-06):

import sys
from PyQt5.QtWidgets import QApplication, QMainWindow, QWidget, QPushButton, QLineEdit
from PyQt5.uic import loadUi
from PyQt5.QtCore import pyqtSignal, QObject, QEventLoop, QTimer, Qt
import serial
import serial.tools.list_ports
import time


class Communicate(QObject):
    buttonClicked = pyqtSignal()


class MainWindow(QMainWindow):  # The main window class of the application that manages the process of graphene coating
    def __init__(self, ui_file, parent=None):
        super().__init__(parent)
        self.setWindowFlags(Qt.WindowMinimizeButtonHint | Qt.CustomizeWindowHint)
        self.ui_file = ui_file
        self.communicate = Communicate()
        self.setup_ui()
        self.setFixedSize(800, 600)
        self.show()
        self.action = 0

    def setup_ui(self):
        self.load_ui()
        self.add_button_handler()

    def load_ui(self):
        loadUi(self.ui_file, self)

    def add_button_handler(self):
        button = self.findChild(QPushButton, "pushButton_2")
        button_2 = self.findChild(QPushButton, "pushButton")
        button_3 = self.findChild(QPushButton, "pushButton_5")
        button_4 = self.findChild(QPushButton, "pushButton_4")
        button_5 = self.findChild(QPushButton, "pushButton_3")

        if button_2:
            button_2.clicked.connect(self.handle_button_click_2)
        if button:
            button.clicked.connect(self.handle_button_click)
        if button_3:
            button_3.clicked.connect(self.handle_button_click_3)
        if button_4:
            button_4.clicked.connect(self.handle_button_click_4)
        if button_5:
            button_5.clicked.connect(self.handle_button_click_5)

    def handle_button_click(self):  # Handler of starting graphene coating proces
        self.communicate.buttonClicked.emit()
        self.action = 1

    def handle_button_click_2(self):  # Handler of closing app button
        self.communicate.buttonClicked.emit()
        sys.exit(0)

    def handle_button_click_3(self):  # Handler of closing app button
        self.communicate.buttonClicked.emit()
        self.action = 2

    def handle_button_click_4(self):  # Handler of closing app button
        self.communicate.buttonClicked.emit()
        self.action = 3

    def handle_button_click_5(self):  # Handler of closing app button
        self.communicate.buttonClicked.emit()
        self.action = 4


class PromptWindow(QWidget):  # The prompt window class with button to continue the process
    def __init__(self, ui_file, parent=None):
        super().__init__(parent)
        self.setWindowFlags(Qt.WindowMinimizeButtonHint | Qt.CustomizeWindowHint)
        self.ui_file = ui_file
        self.communicate = Communicate()
        self.setup_ui()
        self.setFixedSize(410, 120)
        self.show()

    def setup_ui(self):
        self.load_ui()
        self.add_button_handler()

    def load_ui(self):
        loadUi(self.ui_file, self)

    def add_button_handler(self):
        button = self.findChild(QPushButton, "pushButton")
        if button:
            button.clicked.connect(self.handle_button_click)

    def handle_button_click(self):
        self.communicate.buttonClicked.emit()


class ProcessWindow(QWidget):  # Class of processing window
    def __init__(self, ui_file, parent=None):
        super().__init__(parent)
        self.setWindowFlags(Qt.WindowMinimizeButtonHint | Qt.CustomizeWindowHint)
        self.ui_file = ui_file
        self.window = QWidget()
        loadUi(self.ui_file, self)
        self.setFixedSize(410, 120)
        self.show()


def signal_check():  # Check every available port to find connection with Arduino UNO
    available_ports = list(serial.tools.list_ports.comports())

    for port, desc, hwid in available_ports:
        print(desc)
        if "CH340" in desc:
            return port  # If found - return the name of port
    return 0  # If not - return 0


def read_data(ser):  # Function that reads sent data from arduino (from Serial.println())
    buffer = b''  # Init of empty buffer
    timeout = time.time() + 1  # Max wait time for data (2 seconds)

    while time.time() < timeout:
        if ser.in_waiting > 0:
            buffer += ser.read(ser.in_waiting)  # Read of available data
            if b'\n' in buffer:
                line, buffer = buffer.split(b'\n', 1)
                return line.decode('utf-8').strip()

    return None  # If the data haven't been read in time


def detection():  # Function for towrope detection
    try:
        ser = serial.Serial(signal_check(), 9600)
        start_time = time.time()
        duration = 6
        counter = 0
        func_num = "s:"

        while time.time() - start_time < duration:
            ser.write(func_num.encode())
            time.sleep(0.1)
            val = read_data(ser)  # Use a function for non-blocking data flow
            if val is not None:
                val = int(val)
                if val > 340:  # If the value is greater than empty machine - start the process
                    counter = counter + 1
                else:
                    counter = 0
            if counter == 5:
                return True
        return False
    except KeyboardInterrupt:
        ser.close()


def realisation(func_str, event_loop):  # Function that realises each function on arduino by sending the function string and then waiting for ending info
    try:
        ser = serial.Serial(signal_check(), 9600)
        start_time = time.time()
        duration = 9999
        close_flag = 0
        time.sleep(3)
        ser.write(func_str.encode())

        while time.time() - start_time < duration:
            val = read_data(ser)  # Use a function for non-blocking data flow
            print(f"Arduino: {val}")
            ending_info = ["Koniec"]
            if val in ending_info:
                break
    except KeyboardInterrupt:
        pass
    finally:
        if 'ser' in locals() and ser.is_open:
            ser.close()

    event_loop.quit()


def wait_for_signal(win_sel):  # Function waiting for button click to continue the process
    event_loop = QEventLoop()
    win_sel.communicate.buttonClicked.connect(event_loop.quit)
    event_loop.exec_()


def wait_for_arduino(func_str):  # Function waiting for signal from arduino
    event_loop = QEventLoop()
    QTimer.singleShot(100, lambda: realisation(func_str, event_loop))
    event_loop.exec_()
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

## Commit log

2024-01-29 Add new files to project
    Arduino code and excel calculations of sensor calibration function
    [kalibracja_czujnika_maszyny.xlsx]
2024-01-29 Add new elements to project
    Step models of machine and enclosure of electrical components
    [Podstawa.stp, katownik.stp, kolo zebate.stp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]
